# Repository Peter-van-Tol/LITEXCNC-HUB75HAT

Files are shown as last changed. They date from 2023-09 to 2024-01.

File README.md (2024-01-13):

# HUB75HAT

A PCB that turns the Colorlight 5A-75B into an easy to use CNC controller for cheap.

This project ist based on:
- [cyber-murmel/chubby-hat](https://github.com/cyber-murmel/chubby-hat)
- [3k/chubby75](https://github.com/q3k/chubby75/tree/master/5a-75b])

The [HUB75HAT](src/HUB75HAT) is 5A-75B motherboard host for a Raspberry Pi CPU. The HUB75HAT connects to the RPI’s GPIO interface and uses SPI for FPGA communication. Three 26 pin header connectors with standard parallel port pinouts and 5V tolerant I/O are provided for compatibility with most parallel port interfaced motion control / CNC breakout cards / multi axis step motor drives.

In addition to the parallel expansion ports, the HUB75HAT provides two RS-485 interfaces for I/O communication to other RS-485 applications, such as the Huanyang VFD series. These RS-485 are directly taken from the RPI’s header (UART0/1 and UART5).

The firmware is flashed onto the 5A-75B by using the RPI’s GPIO pins. There is no need for external programmers.

The motherboard can also be used _without_ the RPI, by using the standard ethernet communication of the 5A-75B. In this case one would loose the ability to use the RS-485 interfaces and an external tool will be required to flash new firmware.

## Breakout boards (BOB)
Breakout boards are available for the HUB75HAT. These BOBs are designed to add functionality to the HUB75HAT by
extending the GPIO from the 3 26 pin header connectors with drivers, receivers, opto-couplers, etc. Currently the
following BOBs are available:
- [BOB4AXIS](src/BOB4AXIS): Supports driving of 4 axis with differential output. Has inputs for the ALARM of the stepper
  drivers for each axis. Also has optocouplers for homing switches. The homing switches can be either NPN or PNP (selectable
  per axis). Adding this BOB would be enough to run a small 3 axis CNC machine with 1 slave axis.
- [BOB4ENCODER](src/BOB4ENCODER): Supports up to 4 encoders with index (5V only). Unused inputs can be used for generic
  IO. This board also has two connections for SERIAL boards, to further expand GPIO for your machine.

## Serial boards (SERIAL)
These boards are still under development. Goal is to extend GPIO with SPI expanders.

## Releases
The table below gives for each board the current status and the latest release. 

| board | latest release |
|---|---|
| HUB75HAT | [v1.2](src/HUB75HAT/releases/v1.2/) |
| HC245T_BYPASS | [v1.0](src/HC245T_BYPASS//releases/v1.0/) |
| BOB4AXIS | [v1.1](src/BOB4AXIS/releases/v1.1/) |
| BOB4ENCODER | [v1.0](src/BOB4ENCODER/releases/v1.0/) |

In each release folder you'll find a production folder with:
- a .zip-file which can be uploaded to your favorite PCB manufacturer
- a BOM;
- a position file for assembly (only verified for HUB75HAT, the rest is hand-soldered)

## KiCad Version
The following version of KiCad has been used to design the boards:
```
Application: KiCad x64 on x64
Version: 7.0.7, release build
Libraries:
    wxWidgets 3.2.2
    FreeType 2.12.1
    HarfBuzz 6.0.0
    FontConfig 2.14.1
    libcurl/7.88.1-DEV Schannel zlib/1.2.13

Platform: Windows 10 (build 19044), 64-bit edition, 64 bit, Little endian, wxMSW

Build Info:
    Date: Aug 19 2023 13:12:00
    wxWidgets: 3.2.2 (wchar_t,wx containers)
    Boost: 1.81.0
    OCC: 7.7.1
    Curl: 7.88.1-DEV
    ngspice: 40
    Compiler: Visual C++ 1936 without C++ ABI

Build settings:
    KICAD_SPICE=ON
```

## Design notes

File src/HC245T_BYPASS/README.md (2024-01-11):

# `hc245t-bypass`

This tiny board is useful to replace 74HC245T chips on Colorlight 5A-75B and 5A-75E boards.

Don't forget to select Flex board type on the order page!

## Rework

The board needs some rework to improve solderability. It's also possible to solder it "as is", but you can encounter shorts between the adjacent pins.

First, separate the boards from a panel. This can be done easily with scissors.

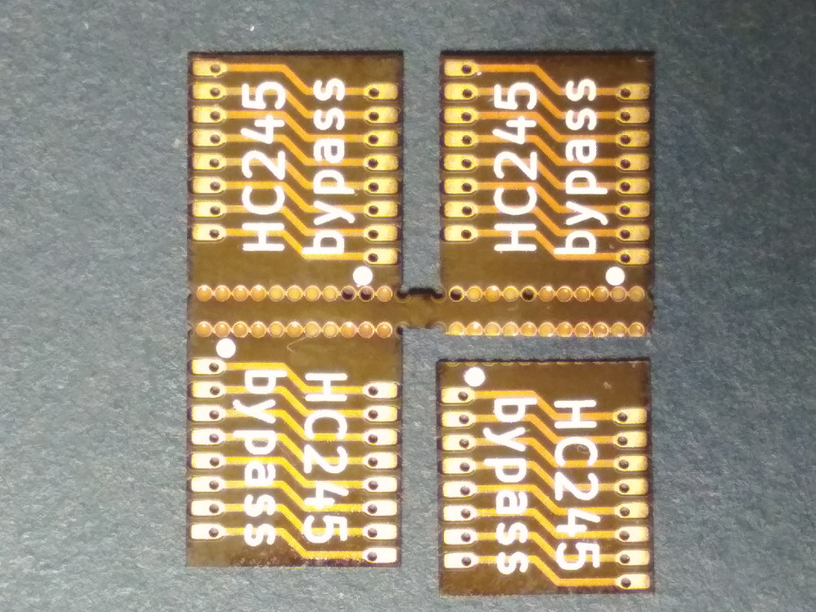
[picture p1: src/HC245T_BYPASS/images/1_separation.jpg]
Board separation


Next, cut each board by the line marked in red. The line should be on the edge of each via, not on the center. Try to make the line as straight as possible. The idea is to cut as much copper as possible, avoiding cutting most of the via copper.

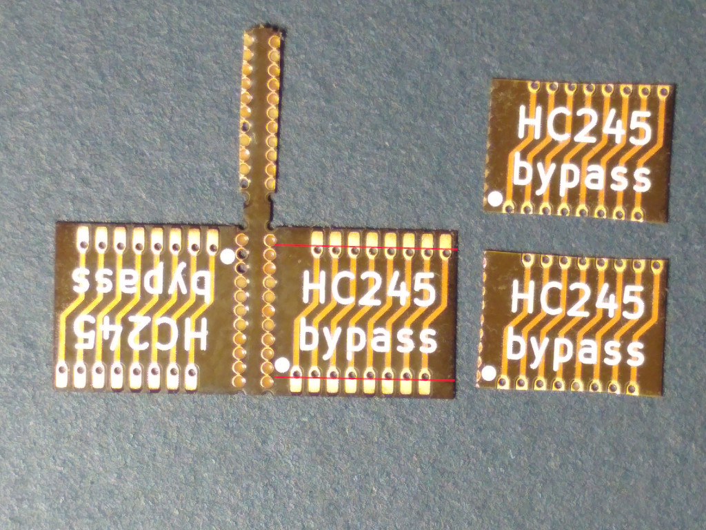
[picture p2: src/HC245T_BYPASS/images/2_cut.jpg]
Rework cut


Now solder it! Note that the first "pin" on the flex board corresponds to the second pin of the 74HC245T footpint.

You can also skip soldering about 50% of 74HC245T footprints by skipping footprints that are used for common signal (like A-E, CLK, LATCH, BLANK) distribution. You can learn in advance which footprints you need to solder and which not. Usually "color" signals are distributed through separate 74HC245T buffers located in groups of 3. Of course, this way you will not be able to control 8 signals out of... many, but it's still a good price for not soldering ~50% of tiny boards.

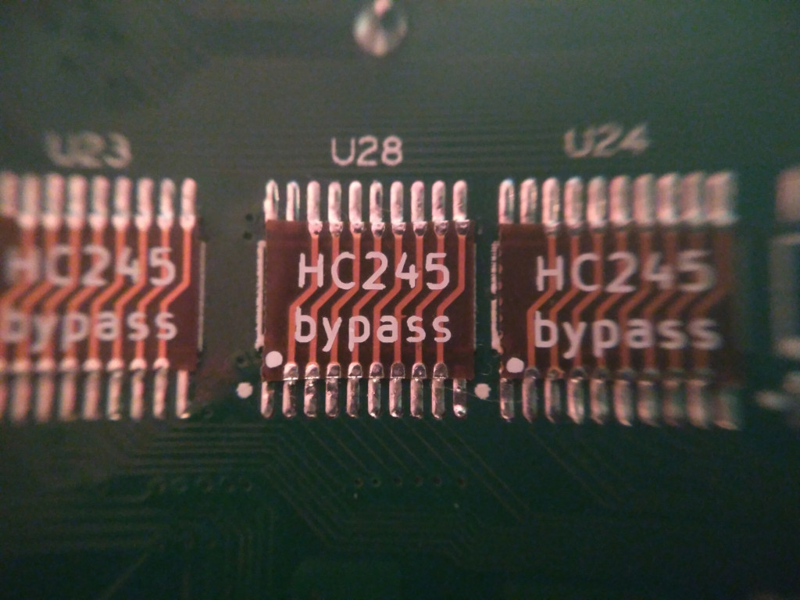
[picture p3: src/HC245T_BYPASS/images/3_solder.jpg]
Solder


Additionally, you can use a continuity tester to check that all "data" pins are connected and adjacent pins are not shorted accidentally. Some of the 74HC245T footpints used for common signal distribution have some of the pins connected together. Check twice: probably your "ringing" footprint has some signals connected on purpose.

## Original work

Shoutouts to [Tom Keddie](https://twitter.com/tom_keddie), who made the [first prototype](https://twitter.com/tom_keddie/status/1233759892164362241) with OSH Park flex board process. Unfortunately, castellated vias on OSH Park flex boards are not officially supported, and they do not guarantee correct manufacturing for such vias. The board in this repo is the improved version of the prototype with the following changes:

* Traces are on both sides of the board instead of only the top side.
* Castellated vias aren't used, instead they are made during the rework process.
* a lot of boards in a panel, instead of 2.
* Smaller silkscreen text that fits between the vias.

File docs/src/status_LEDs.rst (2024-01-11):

===========
Status LEDs
===========

LED locations
=============

The board has three groups of status LEDs:

#. Power and ENA on the bottom-left;
#. TX/RX for RS-489 connnection 1 (UART0/1)
#. TX/RX for RS-489 connnection 5 (UART5)

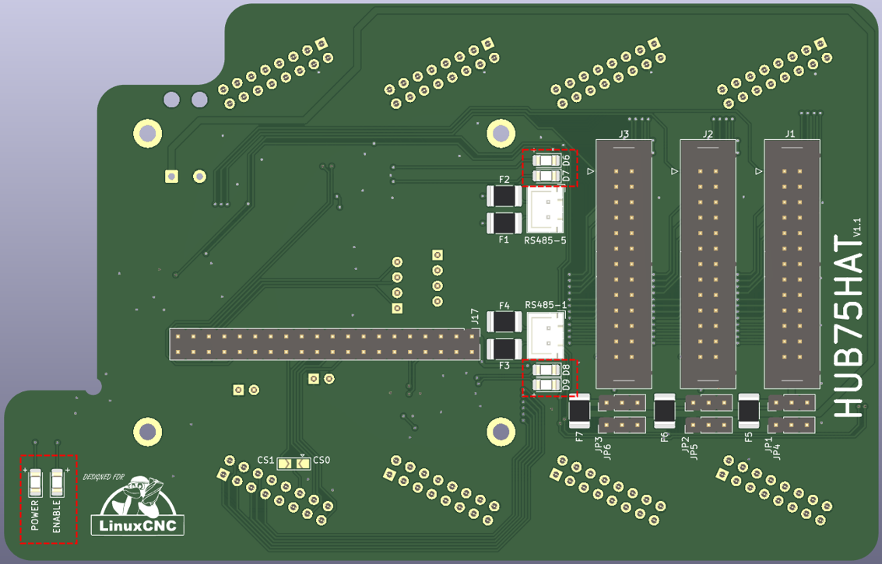
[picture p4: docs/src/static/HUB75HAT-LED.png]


Power, ENA and ESTOP
====================
The power indicator is on when power is supplied to the HUB75HAT (either by the RPi or the
5A-75B). When this LED is on, **DO NOT** unplug the GPIO connector, as this may lead to 
irreversible damage to the RPi and/or 5A-75B.

The ENA indicator is on when the board got the _enable_ command from LinuxCNC. When this LED 
is on, signals from the 5A-75B will flow to the three I/O connectors. It is strongly recommended
not to change connections from the I/O, as this may result in damage or unexpected movement of
the machine.

.. warning::
    In version 1.0 the ENA-LED is not working.

TX/RX status LEDs
=================
Both RS-485 connectors have two LEDs indicating communication to and from the port.

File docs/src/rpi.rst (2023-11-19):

===========================
Preparing your Raspberry-Pi
===========================

This sections describes the steps required to prepare your Raspberry-Pi for running 
LinuxCNC 2.8.4 with the HUB75HAT. You can also choose to use one of the ready-made
images, in which case you can skip these steps. The available images are listed in
the table below.

.. list-table:: Pre-built images for Raspberry-Pi
   :header-rows: 1

   * - Linux version
     - LinuxCNC version
     - username/password
     - link
     - remarks
   * - Debian Buster (32-bit)
     - LinuxCNC 2.8.4
     - cnc/linuxcnc
     - 
     -
   * - Debian Bookworm (64-bit)
     - LinuxCNC 2.9
     - cnc/tuxcnc
     - `link <https://drive.google.com/file/d/1PvfQPvsrcP9Ss2Zrryh35VmkFn31pA4P/view?usp=sharing>`_
     - Read text file on Desktop

Flashing a real-time OS
=======================

Follow these steps to install Debian Buster with a real-time kernel on your
Raspberry-Pi. This recipe has been `posted <https://forum.linuxcnc.org/9-installing-linuxcnc/47841-installing-linuxcnc-2-8-4-on-raspbian-10-buster-tested-on-raspberry-pi-3b-pi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>`_
on the LinuxCNC forum by *elovalvo*.

#. Download from `www.raspberrypi.com <https://www.raspberrypi.com/software/operating-systems/#raspberry-pi-os-legacy>`_
   an image of stable legacy version of Raspberry Pi OS Buster and install to a
   SD card (with Raspberry Pi Imager or similar).
#. Update the OS:

    .. code-block:: bash

        sudo apt update
        sudo apt upgrade

#. Install the realtime kernel (5.15.65-rt49) (source: https://github.com/kdoren/linux/releases):

    .. code-block:: bash

        sudo su     
        cd /tmp     
        wget https://github.com/kdoren/linux/releases/download/rpi_5.15.65-rt49/linux-image-5.15.65-rt49-v7l+_5.15.65-1_armhf.deb     
        apt install ./linux-image-5.15.65-rt49-v7l+_5.15.65-1_armhf.deb     
        KERN=5.15.65-rt49-v7l+      
        mkdir -p /boot/$KERN/o/     
        cp -d /usr/lib/linux-image-$KERN/overlays/* /boot/$KERN/o/     
        cp -dr /usr/lib/linux-image-$KERN/* /boot/$KERN/     
        [[ -d /usr/lib/linux-image-$KERN/broadcom ]] && cp -d /usr/lib/linux-image-$KERN/broadcom/* /boot/$KERN/     
        touch /boot/$KERN/o/README     
        mv /boot/vmlinuz-$KERN /boot/$KERN/     
        mv /boot/initrd.img-$KERN /boot/$KERN/     
        mv /boot/System.map-$KERN /boot/$KERN/     
        cp /boot/config-$KERN /boot/$KERN/     
        cp /boot/cmdline.txt /boot/$KERN/     
        cat >> /boot/config.txt << EOF     

        [all]     
        kernel=vmlinuz-$KERN     
        # initramfs initrd.img-$KERN     
        os_prefix=$KERN/     
        overlay_prefix=o/$(if [[ "$KERN" =~ 'v8' ]]; then echo -e "\narm_64bit=1"; fi)     
        [all]     
        EOF

#. Optimizing kernel (source: https://gnipsel.com/linuxcnc/rpi4-11-emc.html) by opening ``cmdline.txt``

    .. code-block:: bash

        sudo nano /boot/$KERN/cmdline.txt

   And adding ``isolcpus=,2,3 idle=poll`` to the end of the string. To close the file, press
   ``Ctrl+X``, ``y`` and ``Enter``.

We recommend restarting your Raspberry-Pi to ensure that the changes to take effect.

Installing LinuxCNC
===================

Follow these steps to install LinuxCNC 2.8.4. This recipe has been `posted <https://forum.linuxcnc.org/9-installing-linuxcnc/47841-installing-linuxcnc-2-8-4-on-raspbian-10-buster-tested-on-raspberry-pi-3b-pi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>`_
on the LinuxCNC forum by *elovalvo*.

#. Add the LinuxCNC Archive Signing Key to your apt keyring

    .. code-block:: bash

        sudo apt-key adv --keyserver hkp://keyserver.ubuntu.com --recv-key 3cb9fd148f374fef

#. Add the apt repository (`link <http://linuxcnc.org/docs/html/getting-started/getting-linuxcnc.html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>`_):

    .. code-block:: bash

        echo deb http://linuxcnc.org/ buster base 2.8-rtpreempt | sudo tee /etc/apt/sources.list.d/linuxcnc.list
        echo deb-src http://linuxcnc.org/ buster base 2.8-rtpreempt | sudo tee -a /etc/apt/sources.list.d/linuxcnc.list

#. Update the package list from linuxcnc.org and install LinuxCNC

    .. code-block:: bash
        
        sudo apt-get update
        sudo apt-get install linuxcnc-uspace linuxcnc-uspace-dev

Installing LiteX-CNC
====================

Litex-CNC can be installed using ``pip``:

.. code-block:: bash
    
    pip3 install litexcnc[cli] --user

.. note::
    The suffix ``[cli]`` is required to install the command-line interface. Without
    this suffix the scripts referenced in this documentation will not work.

To install the Litex-CNC driver for LinuxCNC, use the following command:

.. code-block:: bash
    
    sudo env "PATH=$PATH" litexcnc install_driver

Optionally, one can also install the toolchain required to build the firmware on the
Raspberry-Pi. When this step is omitted, the firmware has to be compiled on a different
computer.

.. code-block:: bash
    
    litexcnc install_toolchain --user --architecture arm --os linux

.. note::
    This description is specific for Debian Buster, which is a 32-bit operating system.
    When using a newer version of Debian, it might be a 64-bit version, in which case
    the switch ``--architecture arm64`` should be used instead. You can check whether
    you have a 32-bit or a 64-bit operating system by running ``uname -a`` in the terminal.

Enabling SPI
============

The SPI peripheral is not turned on by default. There are two methods to adjust
the settings, either by using the command-line (``raspi-config``) or by using the
GUI.

Using the Desktop GUI
---------------------

You can use the Desktop GUI by heading to the **Pi Start Menu** > **Preferences** > 
**Raspberry Pi Configuration**.

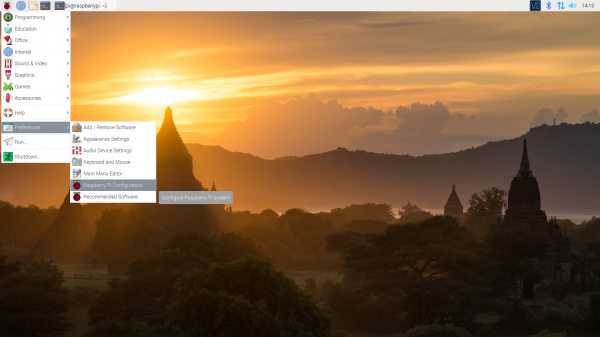
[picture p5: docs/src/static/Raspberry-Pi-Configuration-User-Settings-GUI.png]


A window will pop up with different tabs to adjust settings. What we are interested
is the Interfaces tab. Click on the tab and select Enable for SPI. At this point, you
can enable additional interfaces depending on your project needs. Click on the OK
button to save.

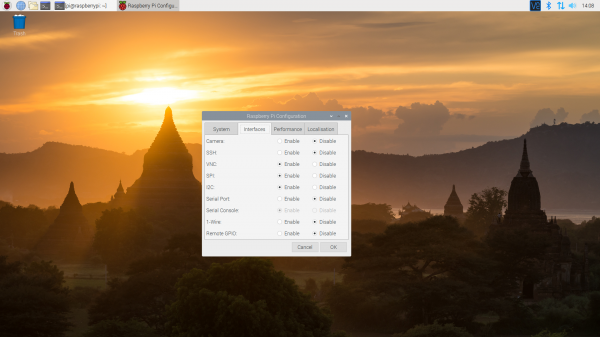
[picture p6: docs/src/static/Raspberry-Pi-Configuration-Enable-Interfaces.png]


We recommend restarting your Pi to ensure that the changes to take effect. Click on 
the **Pi Start Menu** > **Preferences** > **Shutdown**. Since we just need to restart,
click on the Restart button.

Using the command-line
----------------------

If you are using a terminal, you will need to:

#. Run ``sudo raspi-config``.
#. Use the down arrow to select 5 Interfacing Options
#. Arrow down to ``P4 SPI``.
#. Select yes when it asks you to enable SPI,
#. Also select yes if it asks about automatically loading the kernel module.
#. Use the right arrow to select the <Finish> button.
#. Select yes when it asks to reboot.

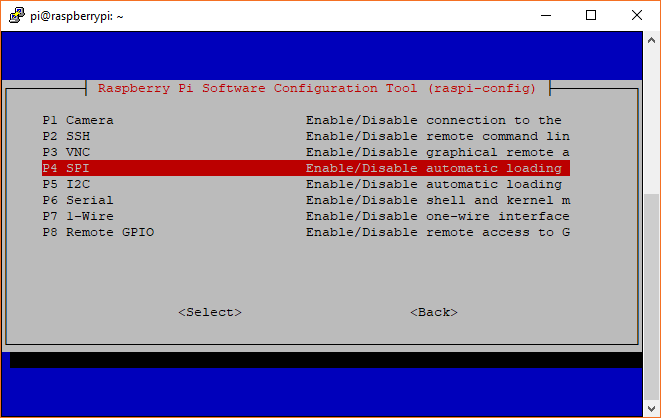
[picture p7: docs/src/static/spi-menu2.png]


The system will reboot. When it comes back up, log in and enter the following command:

.. code-block:: bash

    ls /dev/*spi*

The Pi should respond with::

    /dev/spidev0.0  /dev/spidev0.1

These represent SPI devices on chip enable pins 0 and 1, respectively. These pins are
hardwired within the Pi. Ordinarily, this means the interface supports at most two 
peripherals, but there are cases where multiple devices can be daisy-chained, sharing
a single chip enable signal.

Enabling UART
=============
THe HUB75HAT has two RS-485 connectors, which are powered by the RaspeberryPi UARTs 
0 and 5. To use the RS-485 communication additional steps are required.

UART0
-----

.. info::
    Enabling UART5 is easier than enabling UART1. It is only recommended to enable UART0
    when two RS-485 connections are required.

By default, the primary UART is assigned to the Linux console. If you wish to use the
primary UART for other purposes, you must reconfigure Raspberry Pi OS. This can be done
by using raspi-config:

#. Start raspi-config: ``sudo raspi-config``.
#. Select option 3 - Interface Options.
#. Select option P6 - Serial Port.
#. At the prompt *Would you like a login shell to be accessible over serial?* answer 'No'
#. At the prompt *Would you like the serial port hardware to be enabled?* answer 'Yes'
#. Exit raspi-config and reboot the Raspberry Pi for changes to take effect.

To switch the Bluetooth function to use the mini UART, and makes the first PL011 (UART0) 
the primary UART, add the following lines to ``/boot/config.txt``:

.. code-block::

    enable_uart=1
    dtoverlay=miniuart-bt
    core_freq=250

After rebooting the RaspeberryPi, one can check the whether messages can be sent using UART0
by sending a test-message:

.. code-block:: shell

   sudo echo "Hello world" > /dev/ttyAMA0

Sometimes one can experience ``Permission denied`` problems when executing the command above. In
this case there is most likely another process using UART0. One can disable this service by running
the following command and rebooting the RaspberryPi.

.. code-block:: shell

    sudo systemctl mask serial-getty@ttyAMA0.service

UART5
-----
UART5 is located on GPIO pins 12 (RX) and 13 (TX). To enable UART5 add the following
line to ``/boot/config.txt``:

.. code-block::

    dtoverlay=uart5

UART5 can be found under ``/dev/ttyAMA1``.

Example usage
-------------
An example usage of the UARTs is the `non-realtime component for Huanyang VFDs <https://linuxcnc.org/docs/html/man/man1/hy_vfd.1.html>`_.

.. code-block::

    hy_vfd --device /dev/ttyAMA1

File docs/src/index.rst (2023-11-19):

=================
LITEXCNC-HUB75HAT
=================

A PCB that turns the Colorlight 5A-75B into an easy to use CNC motion controller for cheap. This 
project is based on `q3k/chubby75 <https://github.com/q3k/chubby75/tree/master/5a-75b>`_ and 
`LitexCNC <https://github.com/Peter-van-Tol/LiteX-CNC>`_.

The HUB75HAT is 5A-75B motherboard host for a Raspberry Pi CPU. The HUB75HAT connects to the RPI's
GPIO interface and uses SPI for FPGA communication. Three 26 pin header connectors with standard
parallel port pinouts and 5V tolerant I/O are provided for compatibility with most parallel port 
interfaced motion control / CNC breakout cards / multi axis step motor drives.

In addition to the parallel expansion ports, the HUB75HAT provides two RS-485 interfaces for I/O 
communication to other RS-485 applications, such as the Huanyang VFD series. These RS-485 are directly
taken from the RPI's header (UART0 and UART1).

The firmware is flashed onto the 5A-75B by using the RPI's GPIO pins. There is no need for external
programmers. 

The motherboard can also be used *without* the RPI, by using the standard ethernet communication
of the 5A-75B. In this case one would loose the ability to use the RS-485 interfaces and an external
tool will be required to flash new firmware. 

Contents
========

.. toctree::
   :maxdepth: 2

   Connectors <connectors>
   Status LEDs <status_LEDs>
   Preparing your 5A-75B <5a-75b>
   Preparing your Raspberry-Pi <rpi>
   License <license>
   Changelog <changelog>

Indices and tables
==================

* :ref:`genindex`
* :ref:`modindex`
* :ref:`search`

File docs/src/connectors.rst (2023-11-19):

==========
Connectors
==========

Connector locations
===================

The board contains the following connectors:

- power connector for connecting the HUB75HAT and the 5A-75B
- three connectors for I/O (``J1```, ``J2``, and ``J3``). For each connector one can
  select pull-up or pull-down resistors and whether power should be supplied over the
  connector.
- two RS-485 connectors.



Power
=====
The board can be powered in two ways:

- via the USB-C power supply of the RaspberryPi;
- via the external 5V supply of the 5A-75B.

.. warning::
   When the RaspberryPi and 5A-75B are both powered seperately, the link between the
   HUB75HAT and the 5A-75B should not be connected!

In both cases the 5V supply is shared between the RaspberryPi and the 5A75B via
the link in the top left corner of the board and the GPIO header of the Pi. The
pinout of the power header is:

- pin 1 (located closed to the edge of the board): +5V
- pin 2: GND

I/O Connector pinout
====================
Three 26 pin header connectors with standard parallel port pinouts and 5V tolerant 
I/O are provided for compatibility with most parallel port interfaced motion control / 
CNC breakout cards / multi axis step motor drives.

.. note::
    The FPGA used on the 5a-75B has a 3.3V absolute maximum input voltage specification. 
    To allow interfacing with 5V inputs, the HUB75HAT has bus switches on all I/O pins
    to provide 5V tolerance (`SN74CB3T3245 <https://www.ti.com/product/SN74CB3T3245>`_).

    Note that even though the HUB75HAT can tolerate 5V signal inputs, its outputs will not
    swing to 5V. The outputs are push pull CMOS that will drive to the output supply rail of
    3.3V. This is sufficient for TTL compatibility but may cause problems with some types of
    loads. For example when driving an LED that has its anode connected to 5V, in such
    devices as OPTO isolators and I/O module rack SSRs, the 3.3V high level may not
    completely turn the LED off. To avoid this problem, either drive loads that are ground
    referred, Use 3.3V as the VCC for VCC referred loads, or use open drain mode.

.. warning::
    After power-up or system reset and before the FPGA is configured, the per connector
    pull-up or pull-down resistors will pull all I/O signals per connector to a high or 
    low level. If the FPGA is used for motion control or controlling devices that could 
    present a hazard when enabled, external circuitry should be designed so that this 
    initial state results in a safe condition.

.. csv-table:: Connector I/O-1
   :file: ./tables/IO1.csv
   :widths: 12, 12, 12, 12, 4, 12, 12, 12, 12 
   :header-rows: 1

.. csv-table:: Connector I/O-2
   :file: ./tables/IO2.csv
   :widths: 12, 12, 12, 12, 4, 12, 12, 12, 12 
   :header-rows: 1

.. csv-table:: Connector I/O-3
   :file: ./tables/IO3.csv
   :widths: 12, 12, 12, 12, 4, 12, 12, 12, 12 
   :header-rows: 1

Selection pull-up / pull-down
----------------------------- 
Each I/O connector on the HUB75HAT can have its I/O termination resistors set to pull-up
or pull-down mode. These resistors set the I/O voltage level when the pins are not driven
by the FPGA.

.. info::
   It may be desirable with some parallel port type breakout boards to choose the pulldown
   mode, so that the FPGA outputs are in the low state at power up.

Connector 5V power
------------------ 
The HUB75HAT has the option to supply 5V power to the breakout board. This option is
added to simplify wiring. The option uses 4 parallel cable signals that are normally
used as grounds for supplying 5V to the remote breakout board (DB25 pins 22,23,24 and
25). These pins are AC bypassed on both the HUB75HAT and the breakout cards so do not
compromise AC signal integrity.

The 5V power option is individually selectable for each of the three I/O connectors.
The breakout 5V power is protected by per connector PTC devices (300 mA trip) so will
not cause damage to the HUB75HAT or system if accidentally shorted. This option should
only be enabled for breakout boards or boards specifically wired to accept 5V power on
DB25 pins 22 through 25.

RS-485
======

TODO

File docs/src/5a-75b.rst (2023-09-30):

=====================
Preparing your 5A-75B
=====================

The 5A-75B needs to be modified before it can be used as a CNC motion controller.
The most important changes are:

#. Adding pins for flashing the firmware onto the card (JTAG);
#. Removing the buffers.

Especially the last step requires the removal of several SMD-components from the
card and migth require some experience with soldering these types of components.

Board overview
==============

The image below shows an annotated view of the PCB, showing the JTAG-headers and
the buffers. At this moment there are three known versions of these cards: v6.1,
v7.0 and v8.0. The layout of these cards may differ between versions.

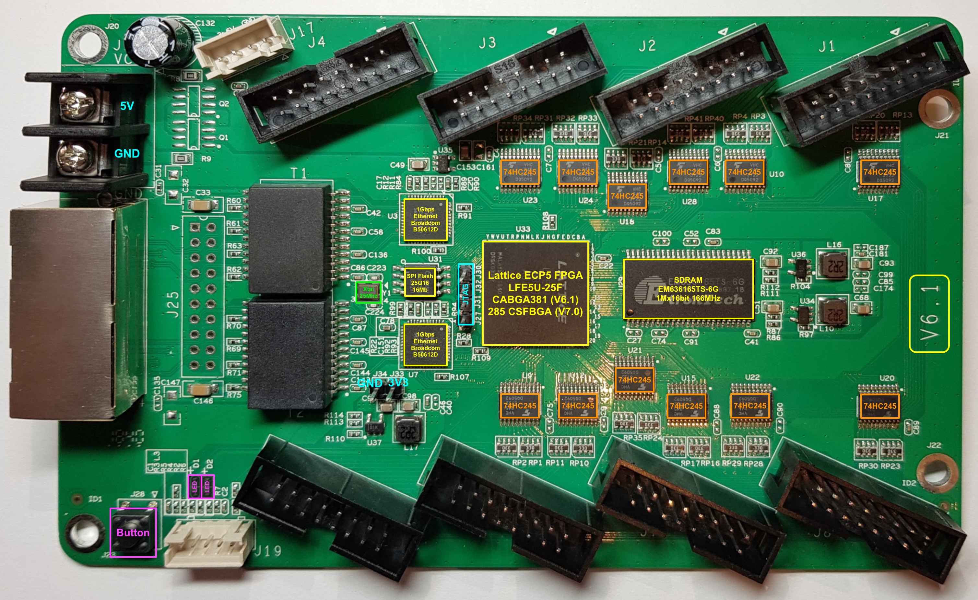
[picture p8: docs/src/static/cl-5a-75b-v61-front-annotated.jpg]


The main difference of the V8.0 card is the location of the JTAG-headers. The HUB75HAT
is designed to accept all versions.

Adding JTAG-headers
===================

The JTAG headers are not populated by default. Solder a 2-pin header at J33/J34 and
a 4-pin header for JTAG next to the FPGA (J27, J31, J32, J30). For the function of
each of the pins, see the `hardware description <https://github.com/q3k/chubby75/blob/master/5a-75b/README.md>`.

Removing the buffers
====================

.. warning::
    All buffers on the board convert the 3.3 V from the FPGA to 5V outputs. Leaving
    the wrong buffers on the board might drive the Raspberry-Pi GPIO with 5 V, leading
    to destruction of the Raspberry-Pi. Therefore it is strongly recommended to remove
    all buffers from the 5A-75B. The HUB75HAT is designed to run on 3.3 V and provides
    5V tolerant buffers in order to protect the FPGA.

The buffers can be removed by any of the methods below:

- desoldering;
- cutting the legs of the ICs with a sharp knife and clearing the pads from the
  left-over pins.

One has to be very carefull

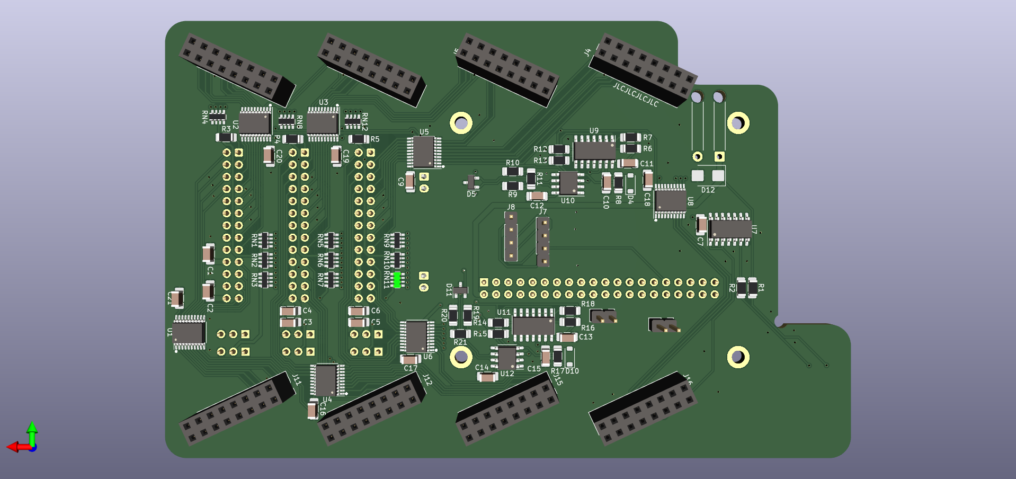
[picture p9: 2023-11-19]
images/LITEXCNC-HUB75HAT_back.png

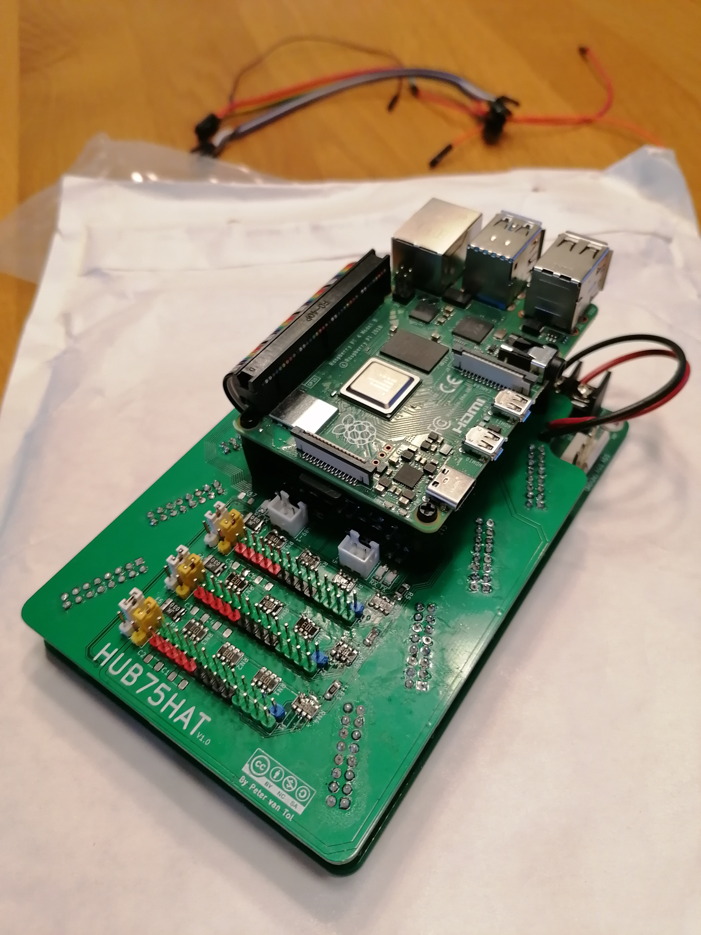
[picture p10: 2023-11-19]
images/HUB75HAT-v1.0.jpg

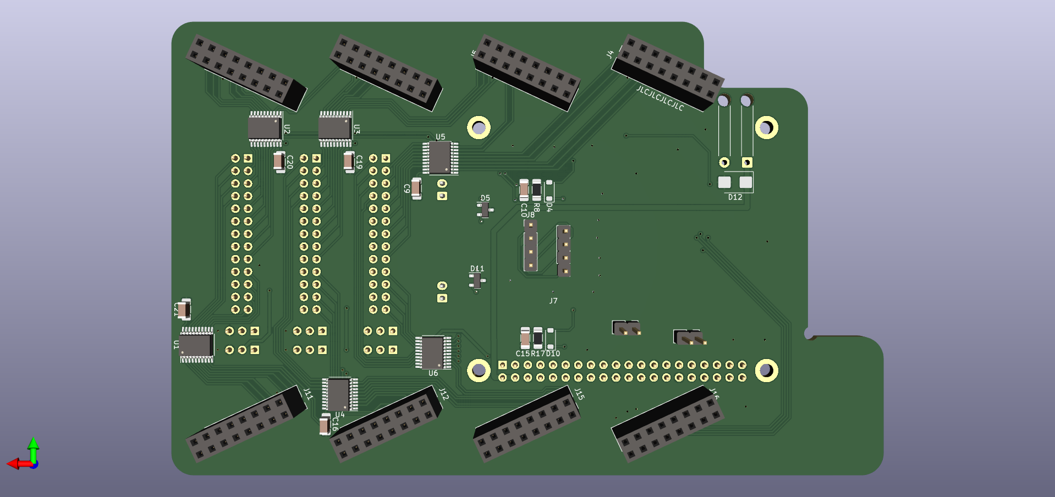
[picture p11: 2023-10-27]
docs/src/images/LITEXCNC-HUB75HAT-back.png

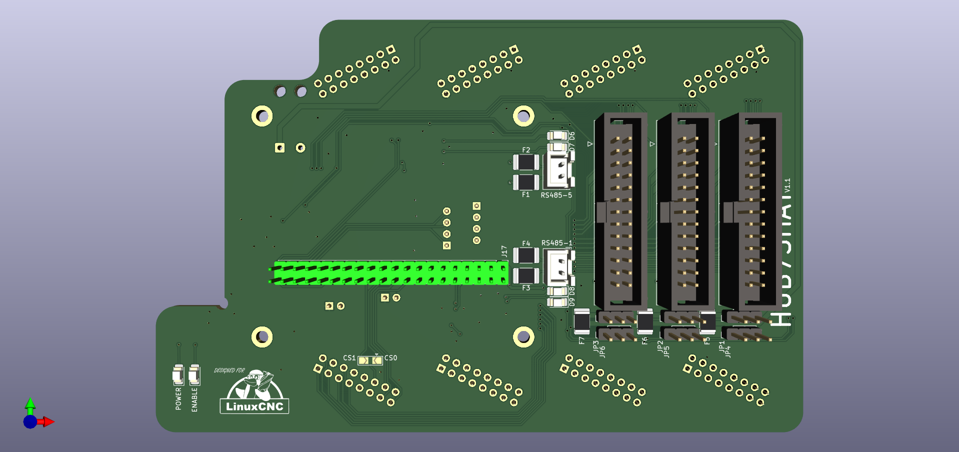
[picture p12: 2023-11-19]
images/LITEXCNC-HUB75HAT_front.png

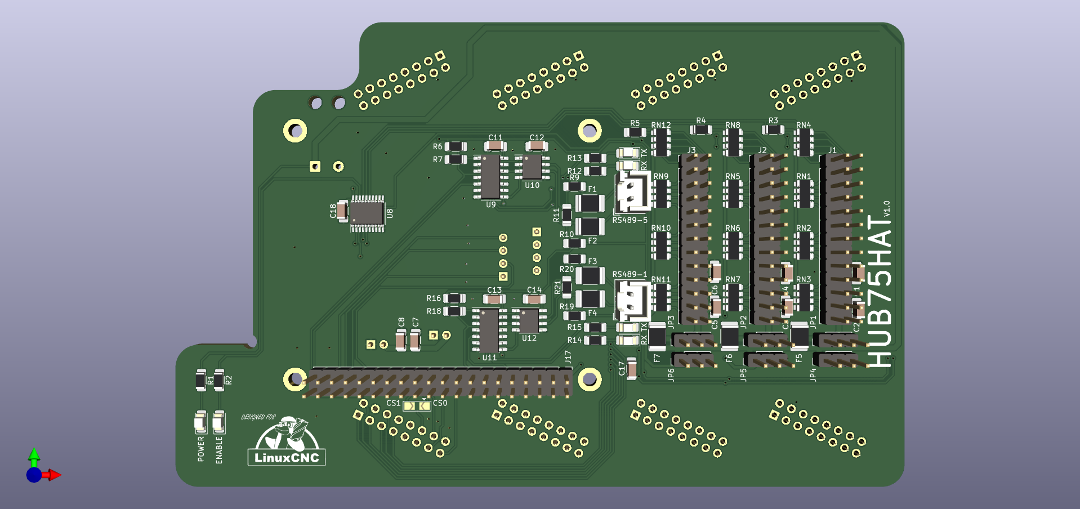
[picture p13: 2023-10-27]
docs/src/images/LITEXCNC-HUB75HAT-front.png

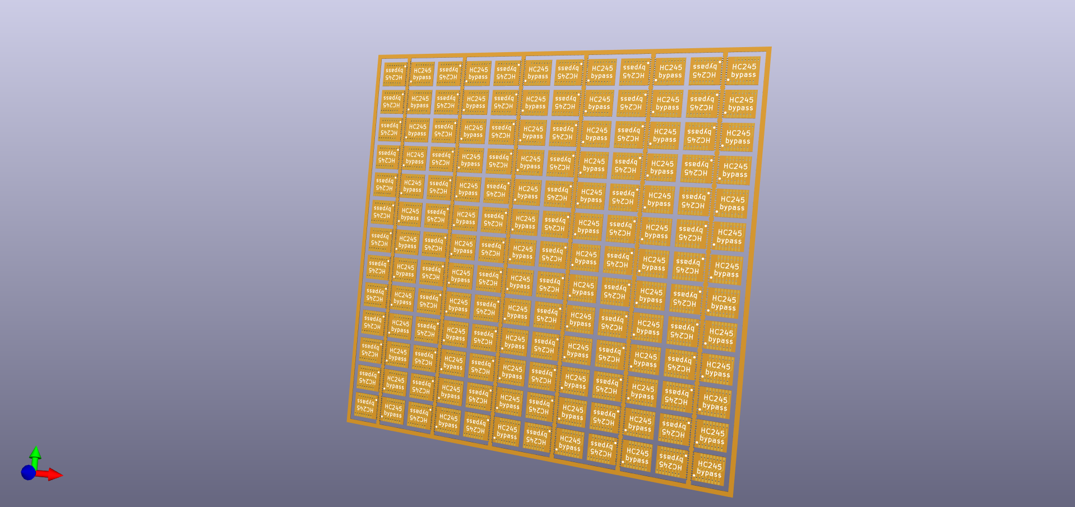
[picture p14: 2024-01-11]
src/HC245T_BYPASS/KICAD/hc245t-bypass-panel.png

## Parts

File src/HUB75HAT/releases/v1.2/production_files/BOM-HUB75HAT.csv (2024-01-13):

Comment | Designator | Footprint | LCSC
74CB3T3245 | U1,U2,U3,U4,U5,U6,U8 | TSSOP-20_4.4x6.5mm_P0.65mm | C15298
33pF | C10,C15 | C_0603_1608Metric_Pad1.08x0.95mm_HandSolder | C1663
150 | R12,R13,R14,R15,R2 | R_0805_2012Metric_Pad1.20x1.40mm_HandSolder | C17471
300 | R1 | R_0805_2012Metric_Pad1.20x1.40mm_HandSolder | C17617
R | R3,R4,R5 | R_1206_3216Metric_Pad1.30x1.75mm_HandSolder | C17902
120 | R11,R21 | R_1206_3216Metric_Pad1.30x1.75mm_HandSolder | C17909
4.7K | R10,R16,R18,R19,R20,R6,R7,R9 | R_1206_3216Metric_Pad1.30x1.75mm_HandSolder | C17936
56k | R17,R8 | R_0603_1608Metric_Pad0.98x0.95mm_HandSolder | C23206
100nF | C1,C11,C12,C13,C14,C16,C17,C18,C19,C2,C20,C21,C3,C4,C5,C6,C7,C9 | C_1206_3216Metric_Pad1.33x1.80mm_HandSolder | C24497
SM712_SOT23 | D11,D5 | SOT-23 | C2687124
CN1J4KTTD1002F | RN1,RN10,RN11,RN12,RN2,RN3,RN4,RN5,RN6,RN7,RN8,RN9 | R_Array_Convex_4x0603_handsolder | C29718
108L | F1,F2,F3,F4,F5,F6,F7 | Fuse_1812_4532Metric_Pad1.30x3.40mm_HandSolder | C782760
MAX3485 | U10,U12 | SOIC-8_3.9x4.9mm_P1.27mm | C8963
Conn_02x20_Odd_Even | J17 | IDC-Header_2x20_P2.54mm_Vertical
Conn_02x13_Odd_Even | J2 | IDC-Header_2x13_P2.54mm_Vertical
LED | D9 | LED_1206_3216Metric_Pad1.42x1.75mm_HandSolder
Jumper_3_Open | JP6 | PinHeader_1x03_P2.54mm_Vertical
LED | D1 | LED_1206_3216Metric_Pad1.42x1.75mm_HandSolder
LED | D6 | LED_1206_3216Metric_Pad1.42x1.75mm_HandSolder
Jumper_3_Open | JP4 | PinHeader_1x03_P2.54mm_Vertical
Jumper_3_Open | JP1 | PinHeader_1x03_P2.54mm_Vertical
LED | D2 | LED_1206_3216Metric_Pad1.42x1.75mm_HandSolder
Jumper_3_Open | JP3 | PinHeader_1x03_P2.54mm_Vertical
SolderJumper_3_Open | JP7 | SolderJumper-3_P2.0mm_Open_TrianglePad1.0x1.5mm
LED | D7 | LED_1206_3216Metric_Pad1.42x1.75mm_HandSolder
Jumper_3_Open | JP5 | PinHeader_1x03_P2.54mm_Vertical
Jumper_3_Open | JP2 | PinHeader_1x03_P2.54mm_Vertical
Conn_02x13_Odd_Even | J3 | IDC-Header_2x13_P2.54mm_Vertical
Conn_02x13_Odd_Even | J1 | IDC-Header_2x13_P2.54mm_Vertical
LED | D8 | LED_1206_3216Metric_Pad1.42x1.75mm_HandSolder
1N4148W | D4 | D_SOD-123
V8.0 | J14 | PinHeader_1x02_P2.54mm_Vertical
74HC04 | U7 | SOIC-14_3.9x8.7mm_P1.27mm
v8.0 | J8 | PinHeader_1x04_P2.54mm_Vertical
HUB75 | J4 | PinSocket_2x08_P2.54mm_Vertical
V7.0 | J13 | PinHeader_1x02_P2.54mm_Vertical
HUB75 | J12 | PinSocket_2x08_P2.54mm_Vertical
HUB75 | J11 | PinSocket_2x08_P2.54mm_Vertical
74HC04 | U9 | SOIC-14_3.9x8.7mm_P1.27mm
74HC04 | U11 | SOIC-14_3.9x8.7mm_P1.27mm
1N4148W | D10 | D_SOD-123
HUB75 | J6 | PinSocket_2x08_P2.54mm_Vertical
HUB75 | J15 | PinSocket_2x08_P2.54mm_Vertical
v7.0 | J7 | PinHeader_1x04_P2.54mm_Vertical
HUB75 | J16 | PinSocket_2x08_P2.54mm_Vertical
Conn_01x02 | J10 | SolderWire-0.5sqmm_1x02_P4.6mm_D0.9mm_OD2.1mm_Relief
HUB75 | J5 | PinSocket_2x08_P2.54mm_Vertical
HUB75 | J9 | PinSocket_2x08_P2.54mm_Vertical

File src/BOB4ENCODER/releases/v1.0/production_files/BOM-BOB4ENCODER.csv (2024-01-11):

Comment | Designator | Footprint | LCSC
Conn_02x04_Odd_Even | J6 | PinSocket_2x04_P1.27mm_Horizontal
Conn_02x04_Odd_Even | J7 | PinSocket_2x04_P1.27mm_Horizontal
Screw_Terminal_01x08 | J5 | CONN-TH_8P-P5.08_KF142V-5.08-8P
Jumper_2_Open | JP2 | PinHeader_1x02_P2.54mm_Vertical
Jumper_2_Open | JP7 | PinHeader_1x02_P2.54mm_Vertical
Jumper_2_Open | JP1 | PinHeader_1x02_P2.54mm_Vertical
Screw_Terminal_01x08 | J3 | CONN-TH_8P-P5.08_KF142V-5.08-8P
Jumper_2_Open | JP9 | PinHeader_1x02_P2.54mm_Vertical
Jumper_2_Open | JP11 | PinHeader_1x02_P2.54mm_Vertical
Jumper_2_Open | JP12 | PinHeader_1x02_P2.54mm_Vertical
Jumper_2_Open | JP3 | PinHeader_1x02_P2.54mm_Vertical
MountingHole_Pad | H3 | MountingHole_3.2mm_M3_Pad_Via
MountingHole_Pad | H1 | MountingHole_3.2mm_M3_Pad_Via
Jumper_2_Open | JP10 | PinHeader_1x02_P2.54mm_Vertical
MountingHole_Pad | H4 | MountingHole_3.2mm_M3_Pad_Via
Screw_Terminal_01x08 | J2 | CONN-TH_8P-P5.08_KF142V-5.08-8P
Screw_Terminal_01x08 | J4 | CONN-TH_8P-P5.08_KF142V-5.08-8P
MountingHole_Pad | H2 | MountingHole_3.2mm_M3_Pad_Via
Jumper_2_Open | JP4 | PinHeader_1x02_P2.54mm_Vertical
Jumper_2_Open | JP5 | PinHeader_1x02_P2.54mm_Vertical
Conn_02x13_Odd_Even | J1 | IDC-Header_2x13_P2.54mm_Vertical
Jumper_2_Open | JP8 | PinHeader_1x02_P2.54mm_Vertical
Jumper_2_Open | JP6 | PinHeader_1x02_P2.54mm_Vertical
AM26LV32xD | U2 | SOIC-16_3.9x9.9mm_P1.27mm
AM26LV32xD | U3 | SOIC-16_3.9x9.9mm_P1.27mm
0.1uF | C3 | C_1206_3216Metric_Pad1.33x1.80mm_HandSolder
AM26LV32xD | U1 | SOIC-16_3.9x9.9mm_P1.27mm
MMSZ5222BT1G | D1 | D_SOD-123
R | R1 | R_1206_3216Metric_Pad1.30x1.75mm_HandSolder
Polyfuse_Small | F1 | R_1812_4532Metric_Pad1.30x3.40mm_HandSolder
0.1uF | C2 | C_1206_3216Metric_Pad1.33x1.80mm_HandSolder
0.1uF | C1 | C_1206_3216Metric_Pad1.33x1.80mm_HandSolder

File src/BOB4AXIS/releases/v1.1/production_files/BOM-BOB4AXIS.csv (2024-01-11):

Comment | Designator | Footprint | LCSC
0.1uF | C1,C2,C3,C4 | C_1206_3216Metric_Pad1.33x1.80mm_HandSolder | C24497
KF142V-5_08-2P | U7 | CONN-TH_P5.08_KF142V-5.08-2P | C475134
AM26LS31CD | U5,U6,U9 | SOIC-16_3.9x9.9mm_P1.27mm | C6179
74HC86 | U8 | SOIC-14_3.9x8.7mm_P1.27mm | C6763
Screw_Terminal_01x08 | J5 | CONN-TH_8P-P5.08_KF142V-5.08-8P
MountingHole_Pad | H3 | MountingHole_3.2mm_M3_Pad_Via
Jumper_3_Open | JP6 | PinHeader_1x03_P2.54mm_Vertical
Screw_Terminal_01x08 | J8 | CONN-TH_8P-P5.08_KF142V-5.08-8P
Jumper_3_Open | JP3 | PinHeader_1x03_P2.54mm_Vertical
Jumper_3_Open | JP8 | PinHeader_1x03_P2.54mm_Vertical
Screw_Terminal_01x03 | J1 | CONN-TH_3P-P5.08_KF142V-5.08-3P
LTV-814 | U3 | DIP-4_W7.62mm
MountingHole_Pad | H1 | MountingHole_3.2mm_M3_Pad_Via
LTV-814 | U1 | DIP-4_W7.62mm
Screw_Terminal_01x08 | J6 | CONN-TH_8P-P5.08_KF142V-5.08-8P
Conn_02x13_Odd_Even | J9 | IDC-Header_2x13_P2.54mm_Vertical
Jumper_3_Open | JP2 | PinHeader_1x03_P2.54mm_Vertical
Jumper_3_Open | JP7 | PinHeader_1x03_P2.54mm_Vertical
Jumper_3_Open | JP4 | PinHeader_1x03_P2.54mm_Vertical
Screw_Terminal_01x03 | J4 | CONN-TH_3P-P5.08_KF142V-5.08-3P
Screw_Terminal_01x03 | J2 | CONN-TH_3P-P5.08_KF142V-5.08-3P
LTV-814 | U4 | DIP-4_W7.62mm
MountingHole_Pad | H2 | MountingHole_3.2mm_M3_Pad_Via
Jumper_3_Open | JP1 | PinHeader_1x03_P2.54mm_Vertical
MountingHole_Pad | H4 | MountingHole_3.2mm_M3_Pad_Via
Screw_Terminal_01x08 | J7 | CONN-TH_8P-P5.08_KF142V-5.08-8P
Screw_Terminal_01x03 | J3 | CONN-TH_3P-P5.08_KF142V-5.08-3P
Jumper_3_Open | JP5 | PinHeader_1x03_P2.54mm_Vertical
LTV-814 | U2 | DIP-4_W7.62mm
10k | R10 | R_1206_3216Metric_Pad1.30x1.75mm_HandSolder
1k | R1 | R_1206_3216Metric_Pad1.30x1.75mm_HandSolder
R | R7 | R_1206_3216Metric_Pad1.30x1.75mm_HandSolder
Polyfuse_Small | F1 | R_1812_4532Metric_Pad1.30x3.40mm_HandSolder
1k | R5 | R_1206_3216Metric_Pad1.30x1.75mm_HandSolder
10k | R12 | R_1206_3216Metric_Pad1.30x1.75mm_HandSolder
10k | R8 | R_1206_3216Metric_Pad1.30x1.75mm_HandSolder
10k | R11 | R_1206_3216Metric_Pad1.30x1.75mm_HandSolder
10k | R4 | R_1206_3216Metric_Pad1.30x1.75mm_HandSolder
10k | R2 | R_1206_3216Metric_Pad1.30x1.75mm_HandSolder
10k | R6 | R_1206_3216Metric_Pad1.30x1.75mm_HandSolder
10k | R9 | R_1206_3216Metric_Pad1.30x1.75mm_HandSolder
1k | R3 | R_1206_3216Metric_Pad1.30x1.75mm_HandSolder
10k | R13 | R_1206_3216Metric_Pad1.30x1.75mm_HandSolder

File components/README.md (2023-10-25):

# Components

This folder contains the parts which are downloaded from third-party resources. A good
source of parts is (https://jlcpcb.com/parts). Parts from this website can be downloaded
and converted to KiCAD using the Python tool `JLC2KiCadLib`:

``` shell
poetry run JLC2KiCadLib C475134  -dir AliExpress -symbol_lib AliExpressSymbols
```

Above statement will:
- download the part `C475134`;
- into the folder `AliExpress`;
- into the symbol file `AliExpressSymbols`.

See for more information the [documentation](https://github.com/TousstNicolas/JLC2KiCad_lib)
of `JLC2KiCadLib`.

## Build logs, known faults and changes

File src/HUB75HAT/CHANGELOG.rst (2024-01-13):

=========
CHANGELOG
=========

Version 1.2 (current version)
=============================

During soldering the version 1.1 boards, the following issues have been identified and solved in this version:
- The 40-pin header has the wrong footprint, there fore it clashes in practice with two polyfuses. The footprint
  will be corrected and the polyfuses will be moved to make space for the 40-pin header.
- Several markings on the board are missing. These will be added to the board.
- Removed unused diode from the board.

Version 1.1
===========

First production version of the board. In total 15 boards were ordered from JLCPCB. The boards were assembled by JLCPCB as well.
The total cost per board was around €17.50 (including shipping and taxes).

The board features:
- Designed for Raspberry Pi 4 and 5 (the older version RPi 3 might also work) with SPI communication
- 3 I/O connectors:
  - each 17 pins of freely addressable inputs / outputs;
  - selectable 10 kOhm pull-down or pull-up resistor;
  - optional 5V power supply on the connector;
- 2 RS-485 connectors for external communications (based on UART0 and UART5 on the Raspberry Pi);
- Resolved issues of board v1.0;
- re-designed with most of the components on the bottom side of the board. This makes the board cheaper to
  produce with services such as JLCPCB. The components to be soldered by hand are on the top side of the board,
  and are limited to: 6 LED's (size 1206), 7 polyfuses (size 1812) and the connectors. 

Version 1.0
===========

Initial version of the board. 

The board features:
- Designed for Raspberry Pi 4 and 5 (the older version RPi 3 might also work) with SPI communication
- 3 I/O connectors:
  - each 17 pins of freely addressable inputs / outputs;
  - selectable 10 kOhm pull-down or pull-up resistor;
  - optional 5V power supply on the connector;
- 2 RS-485 connectors for external communications (based on UART0 and UART5 on the Raspberry Pi)

![HUB75HAT](/images/HUB75HAT-v1.0.jpg)

Known issues:
- the space around the 40 pin connector of the HAT is a bit tight with the mounting points of the RPi. The solution to work with the current board is to use plastic stand-offs and cut part of these away.
- the enable signal should be inverted on the board, because the buffer Output Enable (`OE`) is active LOW. I rather send a HIGH signal to the board to enable it (safety).
- enable LED is not working (can also be a problem with the buffer IC, had some trouble with soldering this buffer). However, even if this LED was working, it would indicate that the board would be disabled (see previous point);
- The 3 I/O headers do not have space for shrouded headers. Instead, I chose to use coloured pin headers to show the different functions of the pins;

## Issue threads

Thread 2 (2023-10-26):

Resistor network size difficult to obtain

Peter-van-Tol, 2023-10-26:
The 1206x4 resistor network is difficult to obtain from AliExpress, or have to revert to Mouser or other supplyers with prohibitive (at least for hobbyist) high prices. These have to be replaced with either smaller components (1206 as total package) or separate resistors.

Peter-van-Tol, 2023-11-06:
Smaller parts might be difficult to solder by hand for DIY-people. Maybe the resistor networks can be duplicated, so for external fabbing the SMD components can be used, while for DIY-enthousiasts the though-hole option is still available.

Peter-van-Tol, 2023-11-06:
Going to be solved in #3

Peter-van-Tol, 2024-01-12:
Solved in version 1.1 of HUB75HAT. Smaller components used, designed to be manufactured by a fab (JLCPCB / PCBWAY / others)

Closed 2024-01-12.

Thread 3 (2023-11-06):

HUB75HAT v1.0: Space around I/O headers insufficient for shrouded header

Peter-van-Tol, 2023-11-06:
The space around the I/O headers is insufficient for shrouded header. In v1.0 this has been solved by applying colored headers showing the functions of the pins. In V1.1 the space should allow for shrouded header:
- The jumpers for power to the connector should be moved down;
- The decoupling capacitors on the power rail should be either moved or flipped to the underside of the board;
- The resistor networks should be either moved or replaced with their through-hole counterpart.

Peter-van-Tol, 2023-11-06:
Going to be solved in #3

Peter-van-Tol, 2024-01-12:
Solved in release [v1. 1] (src/HUB75HAT/releases/v1.1).

Closed 2024-01-12.

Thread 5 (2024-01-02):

Use Release Feature of Github

imvubu, 2024-01-02:
Is it possible to use GitHub releases to segment the various versions of code and board files?

Peter-van-Tol, 2024-01-02:
Thanks for your request. The code is versioned, as it is part of the `litexcnc` codebase and it is placed in the other repository.

A challenge of releasing different versions by GitHub is that this repo contains now 3 boards:
- the HUB75HAT
- the BOB4STEPGEN
- the BOB4ENCODER

It is possible that at one point one of the boards needs an update, while the other remain unchanged. As far as I know, you can have only one release (everything). But if I'm mistaken, please tell me!

How shall the releases be designed:
- by date (everytime a board is updated, all production files will be released);
- by board (each board has its own release history, but not sure whether this is possible)
- other method?

Your input is welcome!

imvubu, 2024-01-11:
Fair point about it containing 3 board,

My request was around wanting to have some boards made and wanting to know knowing that it was past testing

Releases could be based on when a milestone is reached as in you know a board is tested and is working as intended

For me it makes it easier to see what is going on. I may be being a bit pedantic

Peter-van-Tol, 2024-01-11:
At this moment I'm reformatting the repository. Each board will be contained in the `./src` directory and have a dedicated `production` folder in which the production ready versions are published. In the changelog one can see the changes between releases. I expect to finish the work this week.

Peter-van-Tol, 2024-01-11:
Large part of overhaul of the repo is finished. In the README there is a link to latest version of each board.

All current boards have passed testing. Only for HUB75HAT there will be a version 1.2 coming, because the last release there was a problem with the 40-pin header having a clash with a polyfuse. This means that the 40-pin connector has to be soldered manually **and** last, so it rests on top of the polyfuse

Another note is that the HUB75HAT is designed for assembly by JLCPCB (at least, they did it for me, gues other fabs will work similarly). Only the bottom side of the PCB was assembled. The few components remaining on the top side were either unavailable with JLCPCB or very expensive / easy to hand solder.

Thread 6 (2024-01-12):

HUB75HAT V1. 1: 40-pin header clashes with pplyfuses

Peter-van-Tol, 2024-01-12:
40-pin Gpio header has wrong footprint (not shrouded). Therefore the component is clashing with the two polyfuse.

Temporary solved by soldering 40 pin connector on top of polyfuses in order to use the board.

Permanent solution will be correcting the footprint and moving the polyfuses.

Together with this change, the marking CC-NY (license) should be placed on the board again.

Closed 2024-01-13.

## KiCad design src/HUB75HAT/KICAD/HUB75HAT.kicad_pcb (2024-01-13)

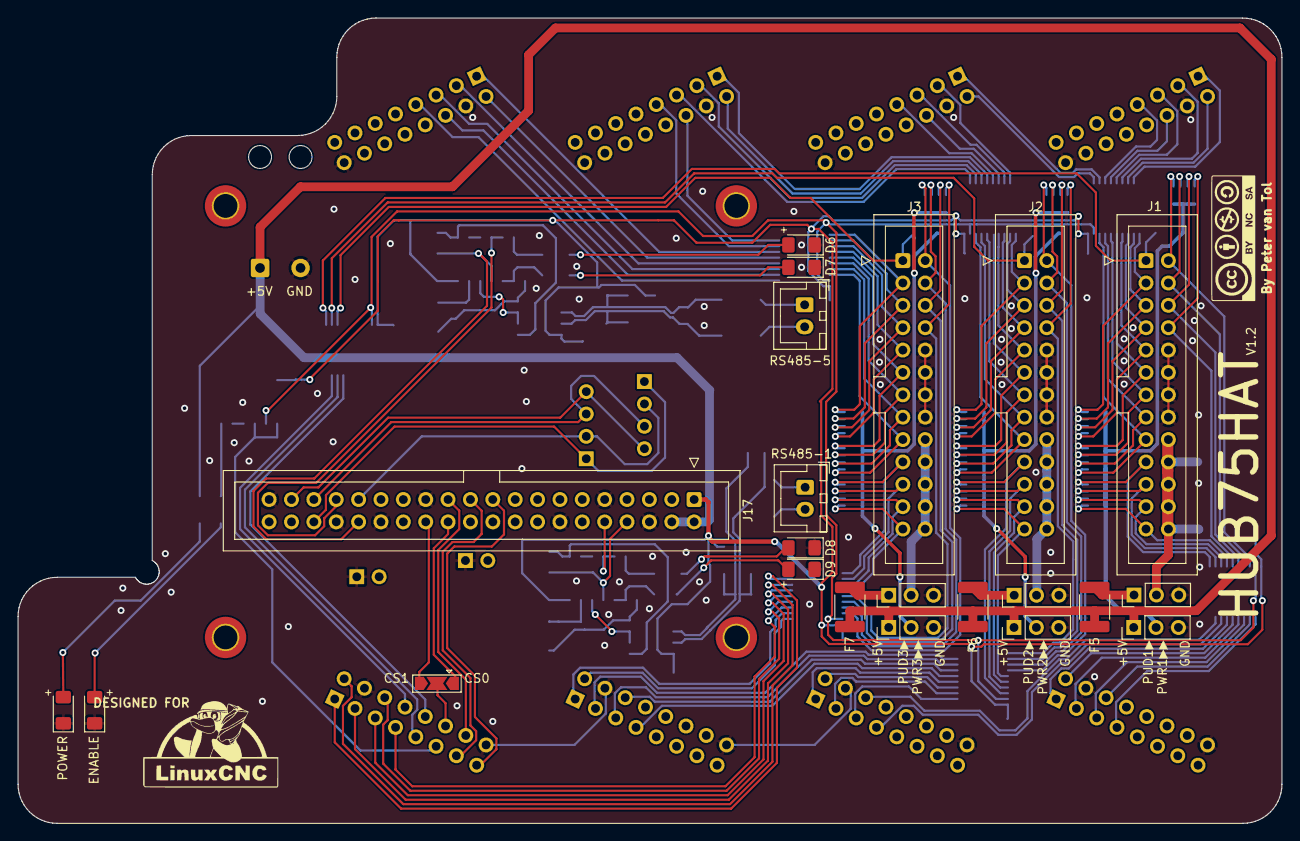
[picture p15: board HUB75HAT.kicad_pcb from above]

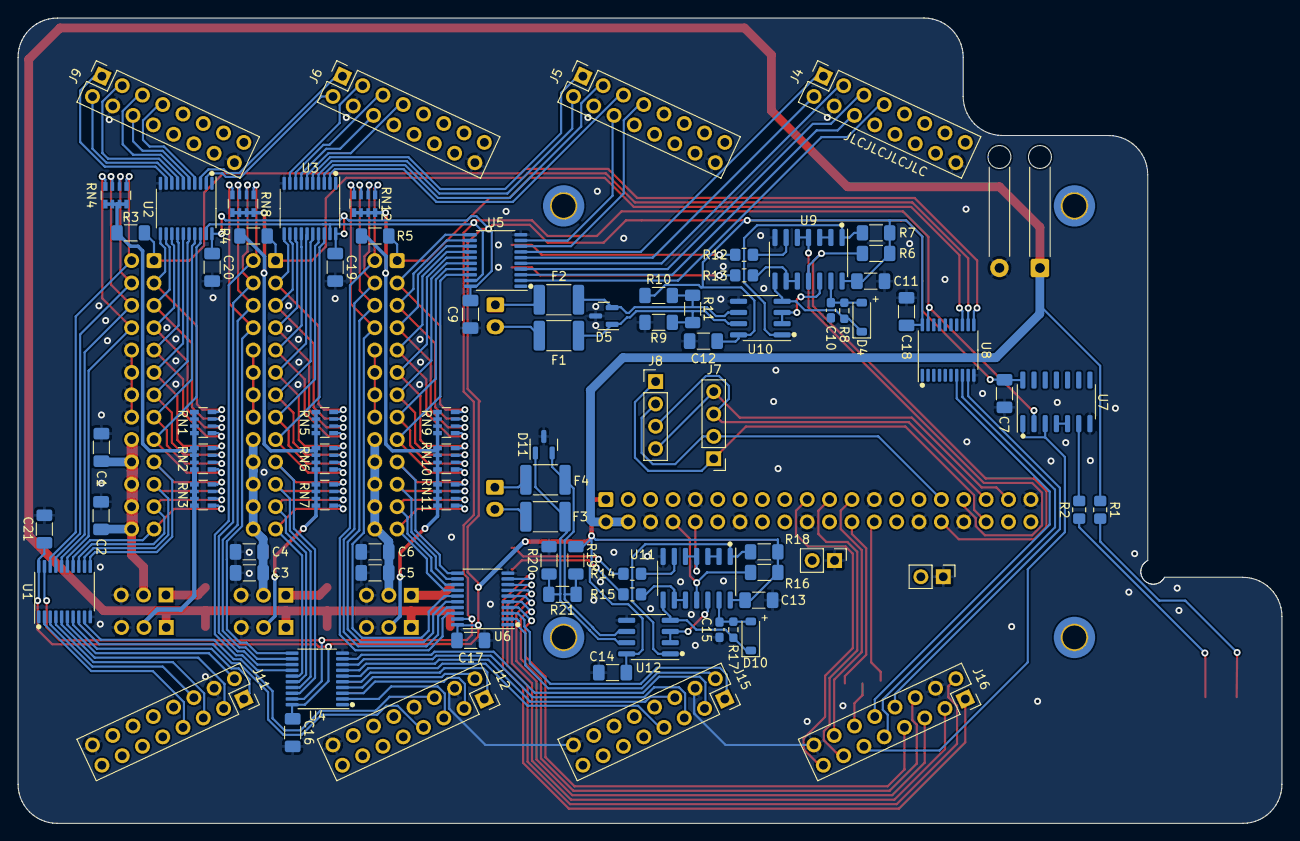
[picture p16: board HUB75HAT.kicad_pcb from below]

Board: 2 copper layers, 143.5 x 91.4 mm, 108 parts (86 on the bottom side), 160 nets.

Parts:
C1, C2, C3, C4, C5, C6, C7, C9, C11, C13, C16, C17, C18, C19, C20, C21: 100nF; C_1206_3216Metric_Pad1.33x1.80mm_HandSolder
C10, C15: 33pF; C_0603_1608Metric_Pad1.08x0.95mm_HandSolder
C12, C14: 0.1uF; C_1206_3216Metric_Pad1.33x1.80mm_HandSolder
D1, D2, D6, D7, D8, D9: LED; LED_1206_3216Metric_Pad1.42x1.75mm_HandSolder
D4, D10: 1N4148W; D_SOD-123
D5, D11: SM712_SOT23; SOT-23
F1, F2, F3, F4, F5, F6, F7: 108L; Fuse_1812_4532Metric_Pad1.30x3.40mm_HandSolder
J1, J2, J3: Conn_02x13_Odd_Even; IDC-Header_2x13_P2.54mm_Vertical
J4, J5, J6, J9, J11, J12, J15, J16: HUB75; PinSocket_2x08_P2.54mm_Vertical
J7: v7.0; PinHeader_1x04_P2.54mm_Vertical
J8: v8.0; PinHeader_1x04_P2.54mm_Vertical
J10: Conn_01x02; SolderWire-0.5sqmm_1x02_P4.6mm_D0.9mm_OD2.1mm_Relief
J13: V7.0; PinHeader_1x02_P2.54mm_Vertical
J14: V8.0; PinHeader_1x02_P2.54mm_Vertical
J17: Conn_02x20_Odd_Even; IDC-Header_2x20_P2.54mm_Vertical
JP1, JP2, JP3, JP4, JP5, JP6: Jumper_3_Open; PinHeader_1x03_P2.54mm_Vertical
JP7: SolderJumper_3_Open; SolderJumper-3_P2.0mm_Open_TrianglePad1.0x1.5mm
R1: 300; R_0805_2012Metric_Pad1.20x1.40mm_HandSolder
R2, R12, R13, R14, R15: 150; R_0805_2012Metric_Pad1.20x1.40mm_HandSolder
R3, R4, R5: R; R_1206_3216Metric_Pad1.30x1.75mm_HandSolder
R6, R16: 4.7k; R_1206_3216Metric_Pad1.30x1.75mm_HandSolder
R7, R9, R10, R18, R19, R20: 4.7K; R_1206_3216Metric_Pad1.30x1.75mm_HandSolder
R8, R17: 56k; R_0603_1608Metric_Pad0.98x0.95mm_HandSolder
R11, R21: 120; R_1206_3216Metric_Pad1.30x1.75mm_HandSolder
RN1, RN2, RN3, RN4, RN5, RN6, RN7, RN8, RN9, RN10, RN11, RN12: CN1J4KTTD1002F; R_Array_Convex_4x0603_handsolder
RS485-1, RS485-5: Conn_01x02_Pin; JST_XH_B2B-XH-A_1x02_P2.50mm_Vertical
U1, U2, U3, U4, U5, U6, U8: 74CB3T3245; TSSOP-20_4.4x6.5mm_P0.65mm
U7, U9, U11: 74HC04; SOIC-14_3.9x8.7mm_P1.27mm
U10, U12: MAX3485; SOIC-8_3.9x4.9mm_P1.27mm

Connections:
+3.3V: C7.1, C9.1, C11.1, C12.1, C13.1, C14.1, C16.1, C17.1, C18.1, C19.1, C20.1, C21.1, J17.1, R6.1, R7.1, R10.1, R16.1, R18.1, R19.1, U1.20 (VCC), U2.20 (VCC), U3.20 (VCC), U4.20 (VCC), U5.20 (VCC), U6.20 (VCC), U7.14 (VCC), U8.20 (VCC), U9.14 (VCC), U10.8 (VCC), U11.14 (VCC), U12.8 (VCC)
+5V: F5.1, F6.1, F7.1, J10.1, J17.2, J17.4, JP4.1 (A), JP5.1 (A), JP6.1 (A), R1.1
/JTAG.TCK: J7.1, J8.1, J17.36
/JTAG.TDI: J7.3, J8.3, J17.35
/JTAG.TDO: J7.4, J8.4, J17.37
/JTAG.TMS: J7.2, J8.2, J17.31
ENA: U1.19 (CE), U2.19 (CE), U3.19 (CE), U4.19 (CE), U5.19 (CE), U6.19 (CE), U7.2, U8.19 (CE)
ENA-LED: R2.1, U7.6
ENA_IN: J16.11, U7.1, U7.3
GND: C1.2, C2.2, C3.2, C4.2, C5.2, C6.2, C7.2, C9.2, C10.2, C11.2, C12.2, C13.2, C14.2, C15.2, C16.2, C17.2, C18.2, C19.2, C20.2, C21.2, D1.1 (K), D2.1 (K), D5.3 (common), D6.1 (K), D7.1 (K), D8.1 (K), D9.1 (K), D11.3 (common), J1.10, J1.12, J1.14, J1.16, J2.10, J2.12, J2.14, J2.16, J3.10, J3.12, J3.14, J3.16, J4.4, J4.16, J5.4, J5.16, J6.4, J6.16, J9.4, J9.16, J10.2, J11.4, J11.16, J12.4, J12.16, J13.1, J14.1, J15.4, J15.16, J16.4, J16.16, J17.6, J17.9, J17.14, J17.20, J17.25, J17.30, J17.34, J17.39, JP1.3 (B), JP2.3 (B), JP3.3 (B), JP4.3 (B), JP5.3 (B), JP6.3 (B), R9.2, R20.2, U1.10 (GND), U2.10 (GND), U3.10 (GND), U4.10 (GND), U5.10 (GND), U6.10 (GND), U7.7 (GND), U8.10 (GND), U9.7 (GND), U10.5 (GND), U11.7 (GND), U12.5 (GND)
J1:0: J11.1, U1.7 (A5)
J1:1: J11.2, U1.6 (A4)
J1:2: J11.3, U1.5 (A3)
J1:4: J11.5, U1.4 (A2)
J1:5: J11.6, U1.3 (A1)
J1:6: J11.7, U1.2 (A0)
J2:0: J12.1, U4.5 (A3)
J2:1: J12.2, U4.4 (A2)
J2:2: J12.3, U4.3 (A1)
J2:4: J12.5, U4.2 (A0)
J2:5: J12.6, U1.9 (A7)
J2:6: J12.7, U1.8 (A6)
J3:0: J15.1, U6.3 (A1)
J3:1: J15.2, U6.2 (A0)
J3:2: J15.3, U4.9 (A7)
J3:4: J15.5, U4.8 (A6)
J3:5: J15.6, U4.7 (A5)
J3:6: J15.7, U4.6 (A4)
J4:0: J16.1, U6.9 (A7)
J4:1: J16.2, U6.8 (A6)
J4:2: J16.3, U6.7 (A5)
J4:4: J16.5, U6.6 (A4)
J4:5: J16.6, U6.5 (A3)
J4:6: J16.7, U6.4 (A2)
J4:7: J16.8, U8.9 (A7)
J4:8: J16.9, U8.8 (A6)
J4:9: J16.10, U8.7 (A5)
J5:0: J4.1, U5.7 (A5)
J5:1: J4.2, U5.6 (A4)
J5:2: J4.3, U5.5 (A3)
J5:4: J4.5, U5.4 (A2)
J5:5: J4.6, U5.3 (A1)
J5:6: J4.7, U5.2 (A0)
J6:0: J5.1, U3.5 (A3)
J6:1: J5.2, U3.4 (A2)
J6:2: J5.3, U3.3 (A1)
J6:4: J5.5, U3.2 (A0)
J6:5: J5.6, U5.9 (A7)
J6:6: J5.7, U5.8 (A6)
J7:0: J6.1, U2.3 (A1)
J7:1: J6.2, U2.2 (A0)
J7:2: J6.3, U3.9 (A7)
J7:4: J6.5, U3.8 (A6)
J7:5: J6.6, U3.7 (A5)
J7:6: J6.7, U3.6 (A4)
J8:0: J9.1, U2.9 (A7)
J8:1: J9.2, U2.8 (A6)
J8:2: J9.3, U2.7 (A5)
J8:4: J9.5, U2.6 (A4)
J8:5: J9.6, U2.5 (A3)
J8:6: J9.7, U2.4 (A2)
unnamed: D1.2 (A), R1.2
unnamed: D2.2 (A), R2.2
unnamed: C10.1, D4.2 (A), R8.2, U9.13
unnamed: D4.1 (K), R8.1, U9.8, U10.4 (DI)
unnamed: D5.1 (A1), F1.1, R9.1, R11.1, U10.7 (B)
unnamed: D5.2 (A2), F2.2, R10.2, R11.2, U10.6 (A)
unnamed: D6.2 (A), R12.2
unnamed: D7.2 (A), R13.2
unnamed: D8.2 (A), R14.2
unnamed: D9.2 (A), R15.2
unnamed: C15.1, D10.2 (A), R17.2, U11.13
unnamed: D10.1 (K), R17.1, U11.8, U12.4 (DI)
unnamed: D11.1 (A1), F3.1, R20.1, R21.1, U12.7 (B)
unnamed: D11.2 (A2), F4.2, R19.2, R21.2, U12.6 (A)
unnamed: F2.1, RS485-5.1
unnamed: F1.2, RS485-5.2
unnamed: F4.1, RS485-1.1
unnamed: F3.2, RS485-1.2
unnamed: F5.2, JP1.1 (A)
unnamed: F6.2, JP2.1 (A)
unnamed: F7.2, JP3.1 (A)
unnamed: JP4.2 (C), R3.2, RN1.1 (R1.1), RN1.2 (R2.1), RN1.3 (R3.1), RN1.4 (R4.1), RN2.1 (R1.1), RN2.2 (R2.1), RN2.3 (R3.1), RN2.4 (R4.1), RN3.1 (R1.1), RN3.2 (R2.1), RN3.3 (R3.1), RN3.4 (R4.1), RN4.1 (R1.1), RN4.2 (R2.1), RN4.3 (R3.1), RN4.4 (R4.1)
unnamed: JP5.2 (C), R4.2, RN5.1 (R1.1), RN5.2 (R2.1), RN5.3 (R3.1), RN5.4 (R4.1), RN6.1 (R1.1), RN6.2 (R2.1), RN6.3 (R3.1), RN6.4 (R4.1), RN7.1 (R1.1), RN7.2 (R2.1), RN7.3 (R3.1), RN7.4 (R4.1), RN8.1 (R1.1), RN8.2 (R2.1), RN8.3 (R3.1), RN8.4 (R4.1)
unnamed: JP6.2 (C), R5.2, RN9.1 (R1.1), RN9.2 (R2.1), RN9.3 (R3.1), RN9.4 (R4.1), RN10.1 (R1.1), RN10.2 (R2.1), RN10.3 (R3.1), RN10.4 (R4.1), RN11.1 (R1.1), RN11.2 (R2.1), RN11.3 (R3.1), RN11.4 (R4.1), RN12.1 (R1.1), RN12.2 (R2.1), RN12.3 (R3.1), RN12.4 (R4.1)
unnamed: R12.1, U9.6
unnamed: R13.1, U9.9, U9.10
unnamed: R14.1, U11.6
unnamed: R15.1, U11.9, U11.10
unnamed: U7.4, U7.5
unnamed: U9.2, U9.3
unnamed: U9.12, U10.2 (~RE), U10.3 (DE)
unnamed: R7.2, U9.1, U10.1 (RO)
unnamed: U11.2, U11.3
unnamed: U11.12, U12.2 (~RE), U12.3 (DE)
unnamed: R18.2, U11.1, U12.1 (RO)
PORTA1: J1.1, R3.1, U8.11 (B7)
PORTA2: J1.3, RN1.8 (R1.2), U2.11 (B7)
PORTA3: J1.5, RN1.7 (R2.2), U2.12 (B6)
PORTA4: J1.7, RN1.6 (R3.2), U2.13 (B5)
PORTA5: J1.9, RN1.5 (R4.2), U2.14 (B4)
PORTA6: J1.11, RN2.8 (R1.2), U2.15 (B3)
PORTA7: J1.13, RN2.7 (R2.2), U2.16 (B2)
PORTA8: J1.15, RN2.6 (R3.2), U2.17 (B1)
PORTA9: J1.17, RN2.5 (R4.2), U2.18 (B0)
PORTA10: J1.19, RN3.8 (R1.2), U1.11 (B7)
PORTA11: J1.21, RN3.7 (R2.2), U1.12 (B6)
PORTA12: J1.23, RN3.6 (R3.2), U1.13 (B5)
PORTA13: J1.25, RN3.5 (R4.2), U1.14 (B4)
PORTA14: J1.2, RN4.5 (R4.2), U1.18 (B0)
PORTA15: J1.4, RN4.6 (R3.2), U1.17 (B1)
PORTA16: J1.6, RN4.7 (R2.2), U1.16 (B2)
PORTA17: J1.8, RN4.8 (R1.2), U1.15 (B3)
PORTB1: J2.1, R4.1, U8.12 (B6)
PORTB2: J2.3, RN5.8 (R1.2), U3.11 (B7)
PORTB3: J2.5, RN5.7 (R2.2), U3.12 (B6)
PORTB4: J2.7, RN5.6 (R3.2), U3.13 (B5)
PORTB5: J2.9, RN5.5 (R4.2), U3.14 (B4)
PORTB6: J2.11, RN6.8 (R1.2), U3.15 (B3)
PORTB7: J2.13, RN6.7 (R2.2), U3.16 (B2)
PORTB8: J2.15, RN6.6 (R3.2), U3.17 (B1)
PORTB9: J2.17, RN6.5 (R4.2), U3.18 (B0)
PORTB10: J2.19, RN7.8 (R1.2), U4.18 (B0)
PORTB11: J2.21, RN7.7 (R2.2), U4.17 (B1)
PORTB12: J2.23, RN7.6 (R3.2), U4.16 (B2)
PORTB13: J2.25, RN7.5 (R4.2), U4.15 (B3)
PORTB14: J2.2, RN8.5 (R4.2), U4.14 (B4)
PORTB15: J2.4, RN8.6 (R3.2), U4.13 (B5)
PORTB16: J2.6, RN8.7 (R2.2), U4.12 (B6)
PORTB17: J2.8, RN8.8 (R1.2), U4.11 (B7)
PORTC1: J3.1, R5.1, U8.13 (B5)
PORTC2: J3.3, RN9.8 (R1.2), U5.11 (B7)
PORTC3: J3.5, RN9.7 (R2.2), U5.12 (B6)
PORTC4: J3.7, RN9.6 (R3.2), U5.13 (B5)
PORTC5: J3.9, RN9.5 (R4.2), U5.14 (B4)
PORTC6: J3.11, RN10.8 (R1.2), U5.15 (B3)
PORTC7: J3.13, RN10.7 (R2.2), U5.16 (B2)
PORTC8: J3.15, RN10.6 (R3.2), U5.17 (B1)
PORTC9: J3.17, RN10.5 (R4.2), U5.18 (B0)
PORTC10: J3.19, RN11.8 (R1.2), U6.11 (B7)
PORTC11: J3.21, RN11.7 (R2.2), U6.12 (B6)
PORTC12: J3.23, RN11.6 (R3.2), U6.13 (B5)
PORTC13: J3.25, RN11.5 (R4.2), U6.14 (B4)
PORTC14: J3.2, RN12.5 (R4.2), U6.18 (B0)
PORTC15: J3.4, RN12.6 (R3.2), U6.17 (B1)
PORTC16: J3.6, RN12.7 (R2.2), U6.16 (B2)
PORTC17: J3.8, RN12.8 (R1.2), U6.15 (B3)
POWOPA: C1.1, C2.1, J1.18, J1.20, J1.22, J1.24, J1.26, JP1.2 (C)
POWOPB: C3.1, C4.1, J2.18, J2.20, J2.22, J2.24, J2.26, JP2.2 (C)
POWOPC: C5.1, C6.1, J3.18, J3.20, J3.22, J3.24, J3.26, JP3.2 (C)
RXD1: J17.10, U11.4, U11.5
RXD5: J17.33, U9.4, U9.5
SPI_CE0: J17.24, JP7.1 (A)
SPI_CE1: J17.26, JP7.3 (B)
SPI_CLCK: J16.14, J17.23
SPI_CS: J16.12, JP7.2 (C)
SPI_MISO: J16.13, J17.21
SPI_MOSI: J16.15, J17.19
TXD1: J17.8, R16.2, U11.11
TXD5: J17.32, R6.2, U9.11

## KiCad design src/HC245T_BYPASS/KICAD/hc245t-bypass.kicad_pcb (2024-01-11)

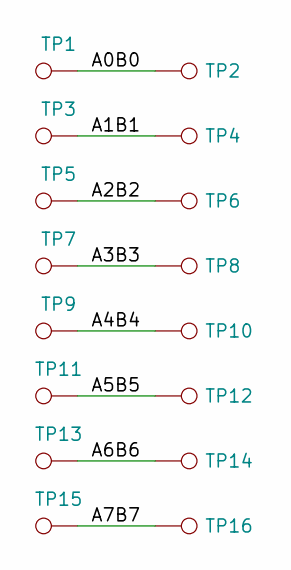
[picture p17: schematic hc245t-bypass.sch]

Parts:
TP1, TP2, TP3, TP4, TP5, TP6, TP7, TP8, TP9, TP10, TP11, TP12, TP13, TP14, TP15, TP16: TestPoint; PAD

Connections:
/A0B0: TP1.1, TP2.1
/A1B1: TP3.1, TP4.1
/A2B2: TP5.1, TP6.1
/A3B3: TP7.1, TP8.1
/A4B4: TP9.1, TP10.1
/A5B5: TP11.1, TP12.1
/A6B6: TP13.1, TP14.1
/A7B7: TP15.1, TP16.1

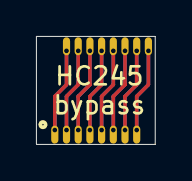
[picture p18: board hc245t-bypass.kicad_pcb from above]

Board: 2 copper layers, 6.6 x 6.0 mm, 16 parts (0 on the bottom side), 8 nets.

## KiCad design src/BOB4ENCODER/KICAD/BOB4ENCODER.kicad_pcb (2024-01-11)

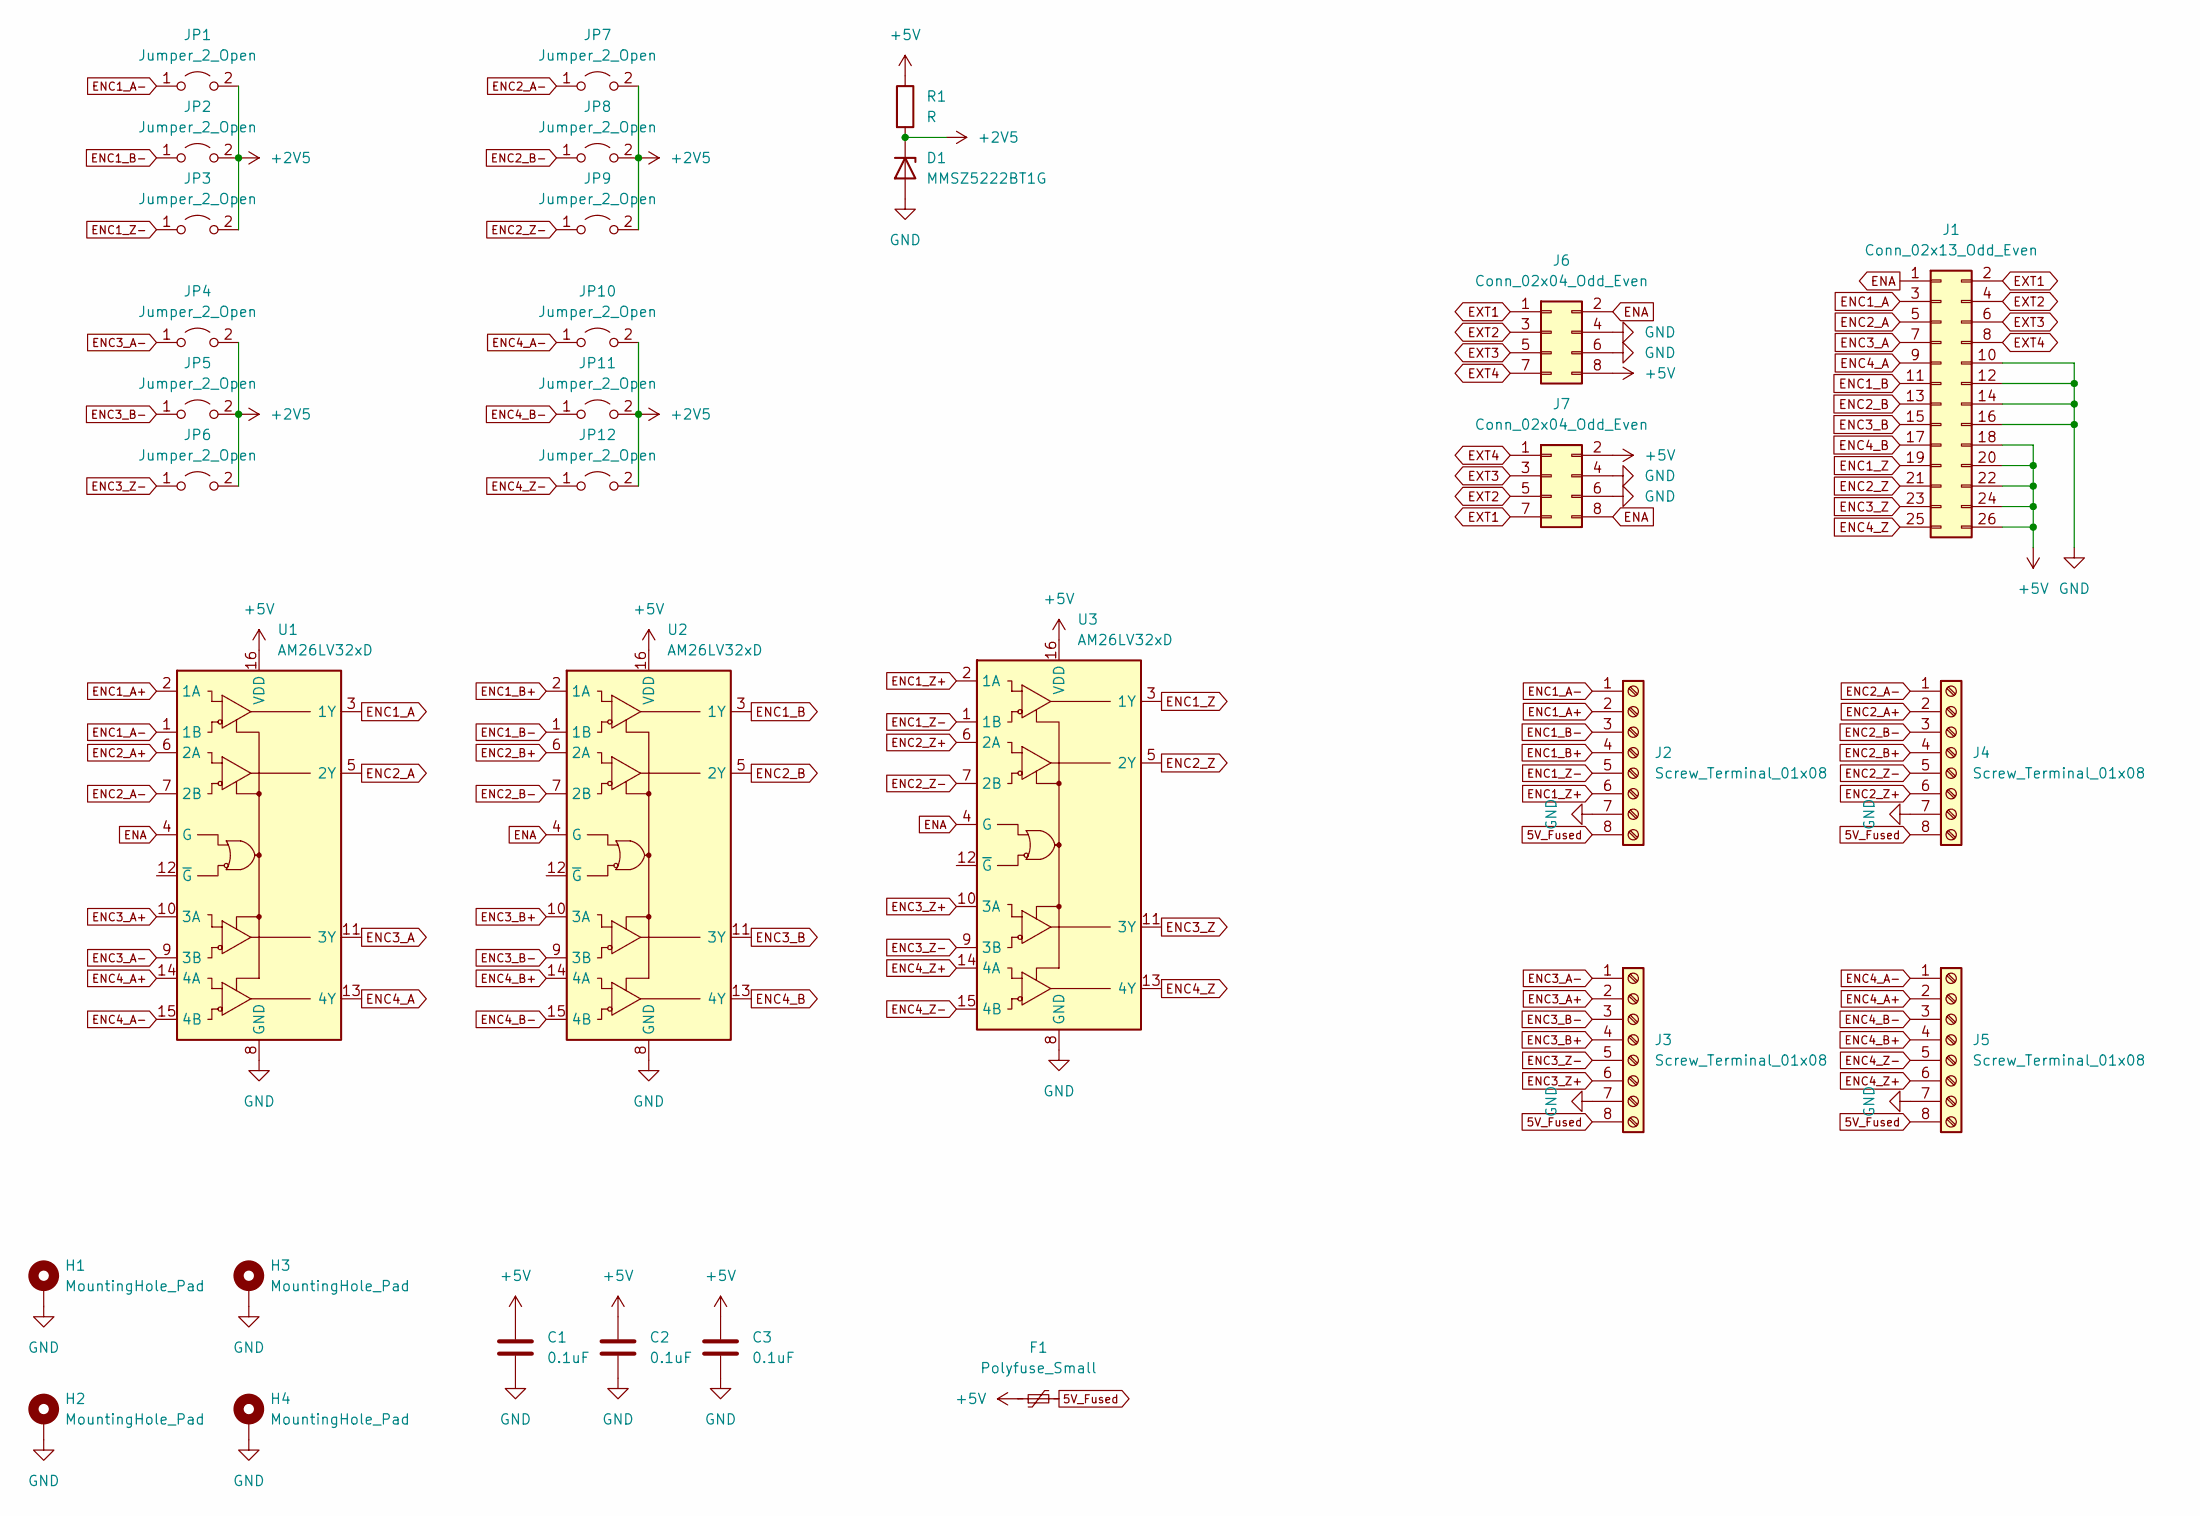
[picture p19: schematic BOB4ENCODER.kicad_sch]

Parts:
C1, C2, C3: 0.1uF; C_1206_3216Metric_Pad1.33x1.80mm_HandSolder
D1: MMSZ5222BT1G; D_SOD-123
F1: Polyfuse_Small; R_1812_4532Metric_Pad1.30x3.40mm_HandSolder
H1, H2, H3, H4: MountingHole_Pad; MountingHole_3.2mm_M3_Pad_Via
J1: Conn_02x13_Odd_Even; IDC-Header_2x13_P2.54mm_Vertical
J2, J3, J4, J5: Screw_Terminal_01x08; CONN-TH_8P-P5.08_KF142V-5.08-8P
J6, J7: Conn_02x04_Odd_Even; PinSocket_2x04_P1.27mm_Horizontal
JP1, JP2, JP3, JP4, JP5, JP6, JP7, JP8, JP9, JP10, JP11, JP12: Jumper_2_Open; PinHeader_1x02_P2.54mm_Vertical
R1: R; R_1206_3216Metric_Pad1.30x1.75mm_HandSolder
U1, U2, U3: AM26LV32xD; SOIC-16_3.9x9.9mm_P1.27mm

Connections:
5V_Fused: F1.2, J2.8, J3.8, J4.8, J5.8
+2V5: D1.1 (K), JP1.2 (B), JP2.2 (B), JP3.2 (B), JP4.2 (B), JP5.2 (B), JP6.2 (B), JP7.2 (B), JP8.2 (B), JP9.2 (B), JP10.2 (B), JP11.2 (B), JP12.2 (B), R1.2
+5V: C1.1, C2.1, C3.1, F1.1, J1.18, J1.20, J1.22, J1.24, J1.26, J6.8, J7.2, R1.1, U1.16 (VDD), U2.16 (VDD), U3.16 (VDD)
ENA: J1.1, J6.2, J7.8, U1.4 (G), U2.4 (G), U3.4 (G)
ENC1_A: J1.3, U1.3 (1Y)
ENC1_A+: J2.2, U1.2 (1A)
ENC1_A-: J2.1, JP1.1 (A), U1.1 (1B)
ENC1_B: J1.11, U2.3 (1Y)
ENC1_B+: J2.4, U2.2 (1A)
ENC1_B-: J2.3, JP2.1 (A), U2.1 (1B)
ENC1_Z: J1.19, U3.3 (1Y)
ENC1_Z+: J2.6, U3.2 (1A)
ENC1_Z-: J2.5, JP3.1 (A), U3.1 (1B)
ENC2_A: J1.5, U1.5 (2Y)
ENC2_A+: J4.2, U1.6 (2A)
ENC2_A-: J4.1, JP7.1 (A), U1.7 (2B)
ENC2_B: J1.13, U2.5 (2Y)
ENC2_B+: J4.4, U2.6 (2A)
ENC2_B-: J4.3, JP8.1 (A), U2.7 (2B)
ENC2_Z: J1.21, U3.5 (2Y)
ENC2_Z+: J4.6, U3.6 (2A)
ENC2_Z-: J4.5, JP9.1 (A), U3.7 (2B)
ENC3_A: J1.7, U1.11 (3Y)
ENC3_A+: J3.2, U1.10 (3A)
ENC3_A-: J3.1, JP4.1 (A), U1.9 (3B)
ENC3_B: J1.15, U2.11 (3Y)
ENC3_B+: J3.4, U2.10 (3A)
ENC3_B-: J3.3, JP5.1 (A), U2.9 (3B)
ENC3_Z: J1.23, U3.11 (3Y)
ENC3_Z+: J3.6, U3.10 (3A)
ENC3_Z-: J3.5, JP6.1 (A), U3.9 (3B)
ENC4_A: J1.9, U1.13 (4Y)
ENC4_A+: J5.2, U1.14 (4A)
ENC4_A-: J5.1, JP10.1 (A), U1.15 (4B)
ENC4_B: J1.17, U2.13 (4Y)
ENC4_B+: J5.4, U2.14 (4A)
ENC4_B-: J5.3, JP11.1 (A), U2.15 (4B)
ENC4_Z: J1.25, U3.13 (4Y)
ENC4_Z+: J5.6, U3.14 (4A)
ENC4_Z-: J5.5, JP12.1 (A), U3.15 (4B)
EXT1: J1.2, J6.1, J7.7
EXT2: J1.4, J6.3, J7.5
EXT3: J1.6, J6.5, J7.3
EXT4: J1.8, J6.7, J7.1
GND: C1.2, C2.2, C3.2, D1.2 (A), H1.1, H2.1, H3.1, H4.1, J1.10, J1.12, J1.14, J1.16, J2.7, J3.7, J4.7, J5.7, J6.4, J6.6, J7.4, J7.6, U1.8 (GND), U2.8 (GND), U3.8 (GND)

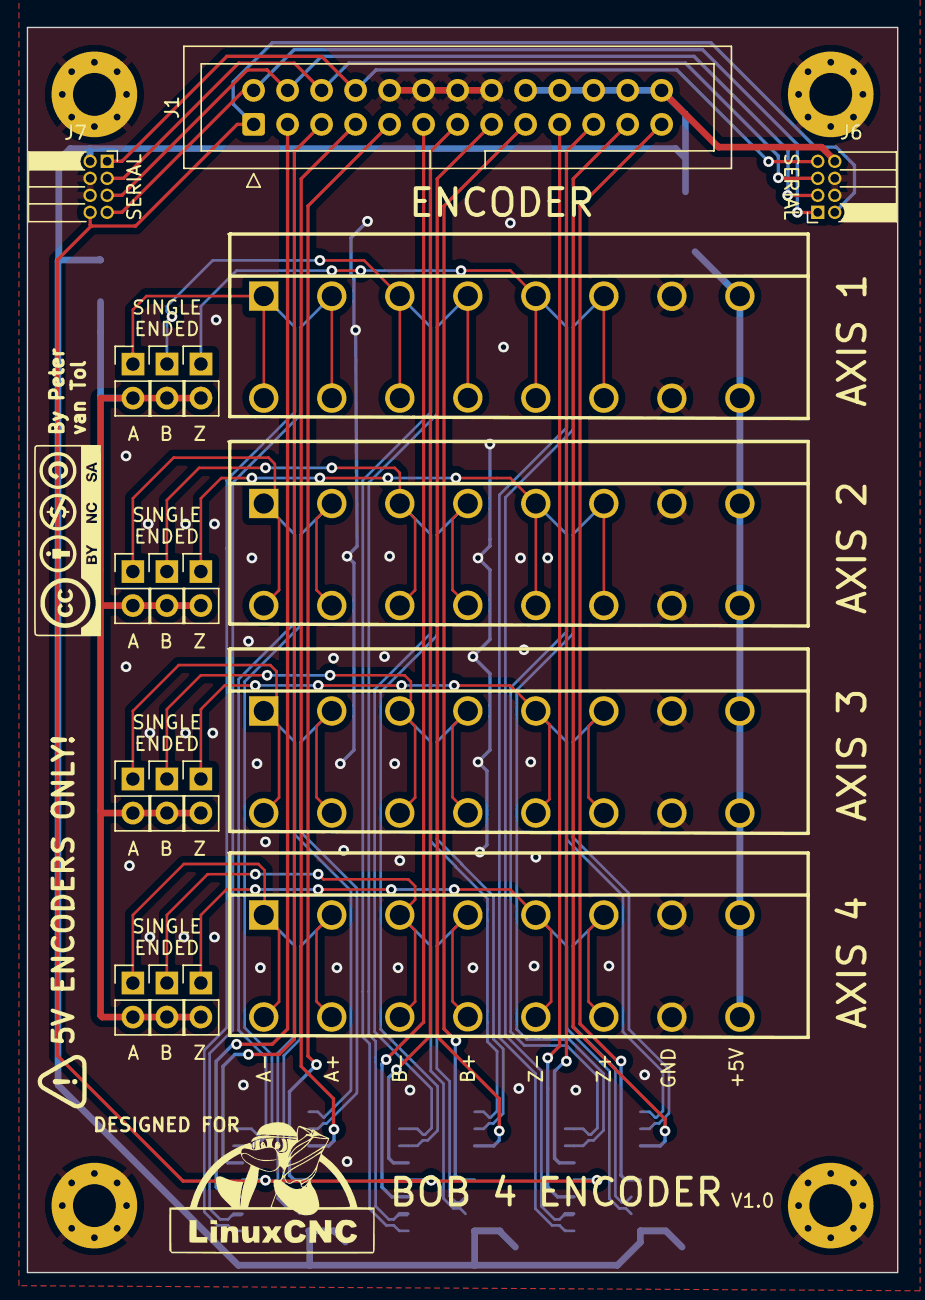
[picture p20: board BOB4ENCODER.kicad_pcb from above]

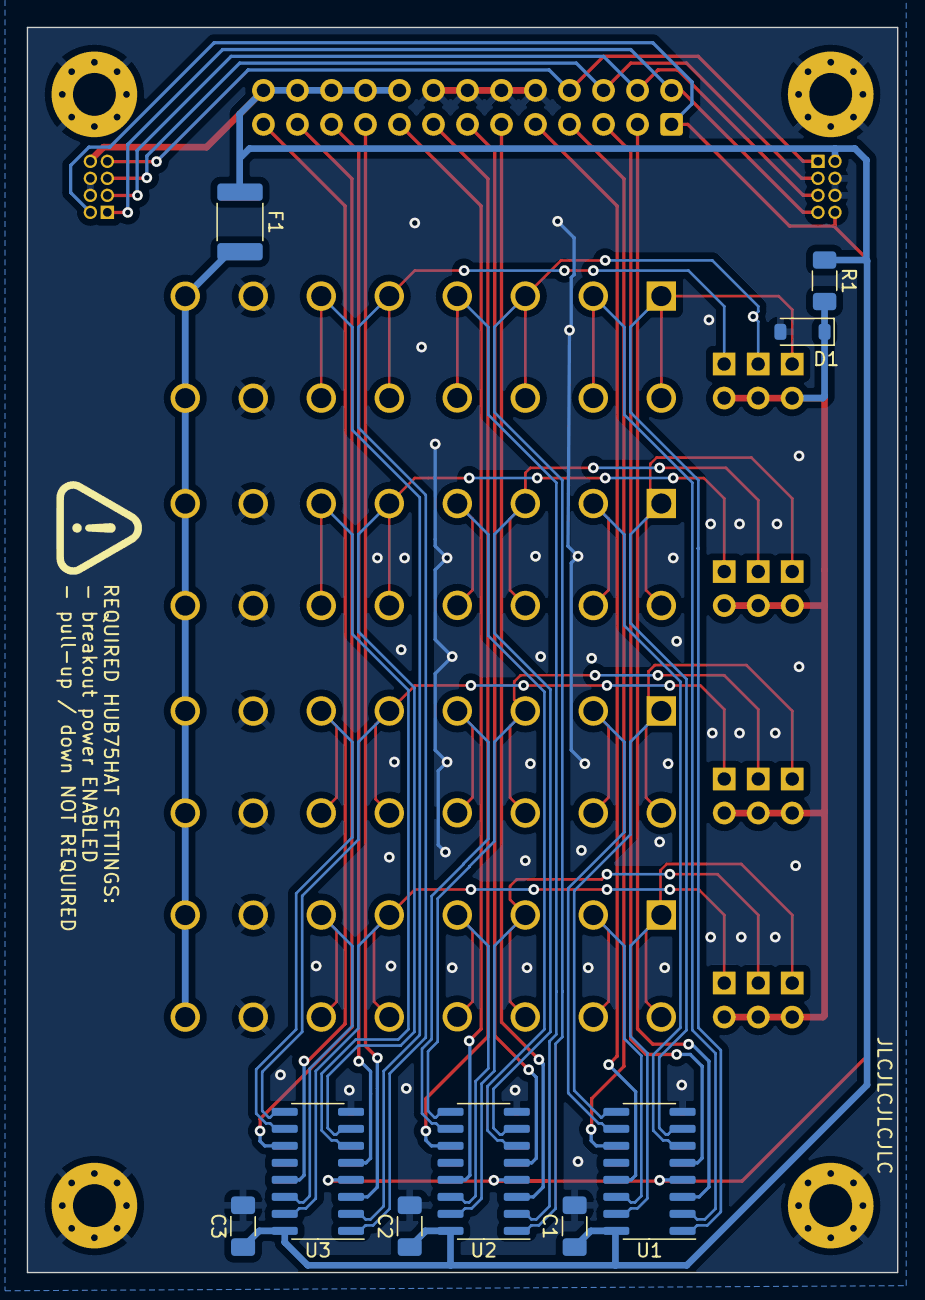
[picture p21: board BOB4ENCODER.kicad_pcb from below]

Board: 2 copper layers, 65.0 x 93.0 mm, 32 parts (9 on the bottom side), 45 nets.

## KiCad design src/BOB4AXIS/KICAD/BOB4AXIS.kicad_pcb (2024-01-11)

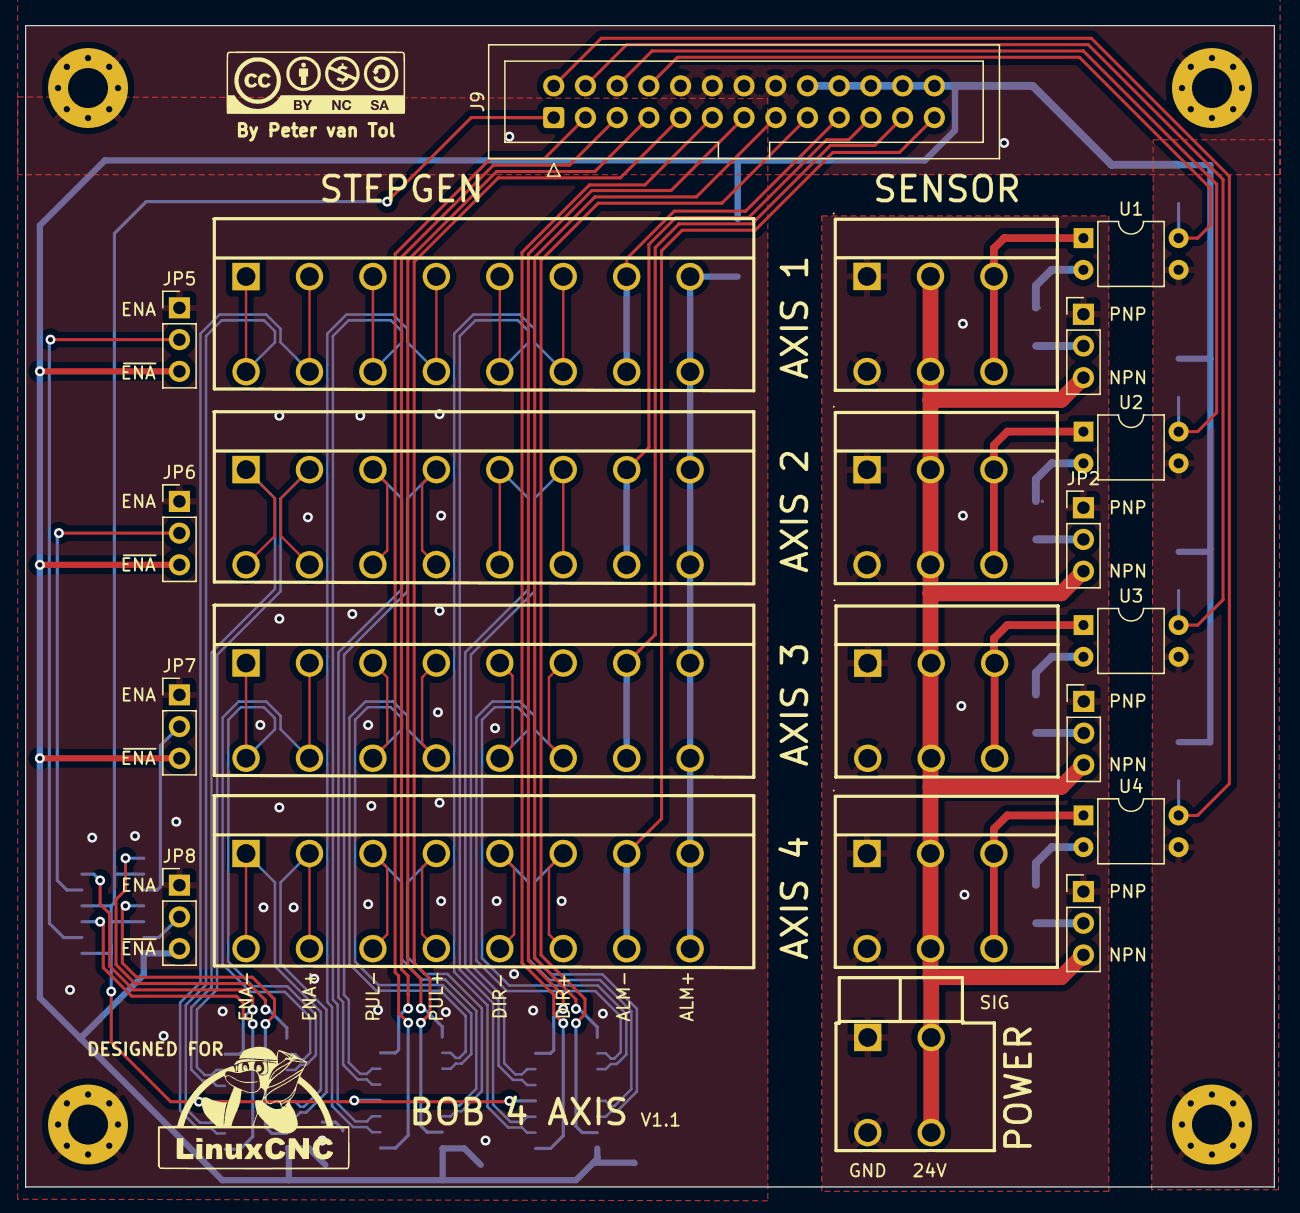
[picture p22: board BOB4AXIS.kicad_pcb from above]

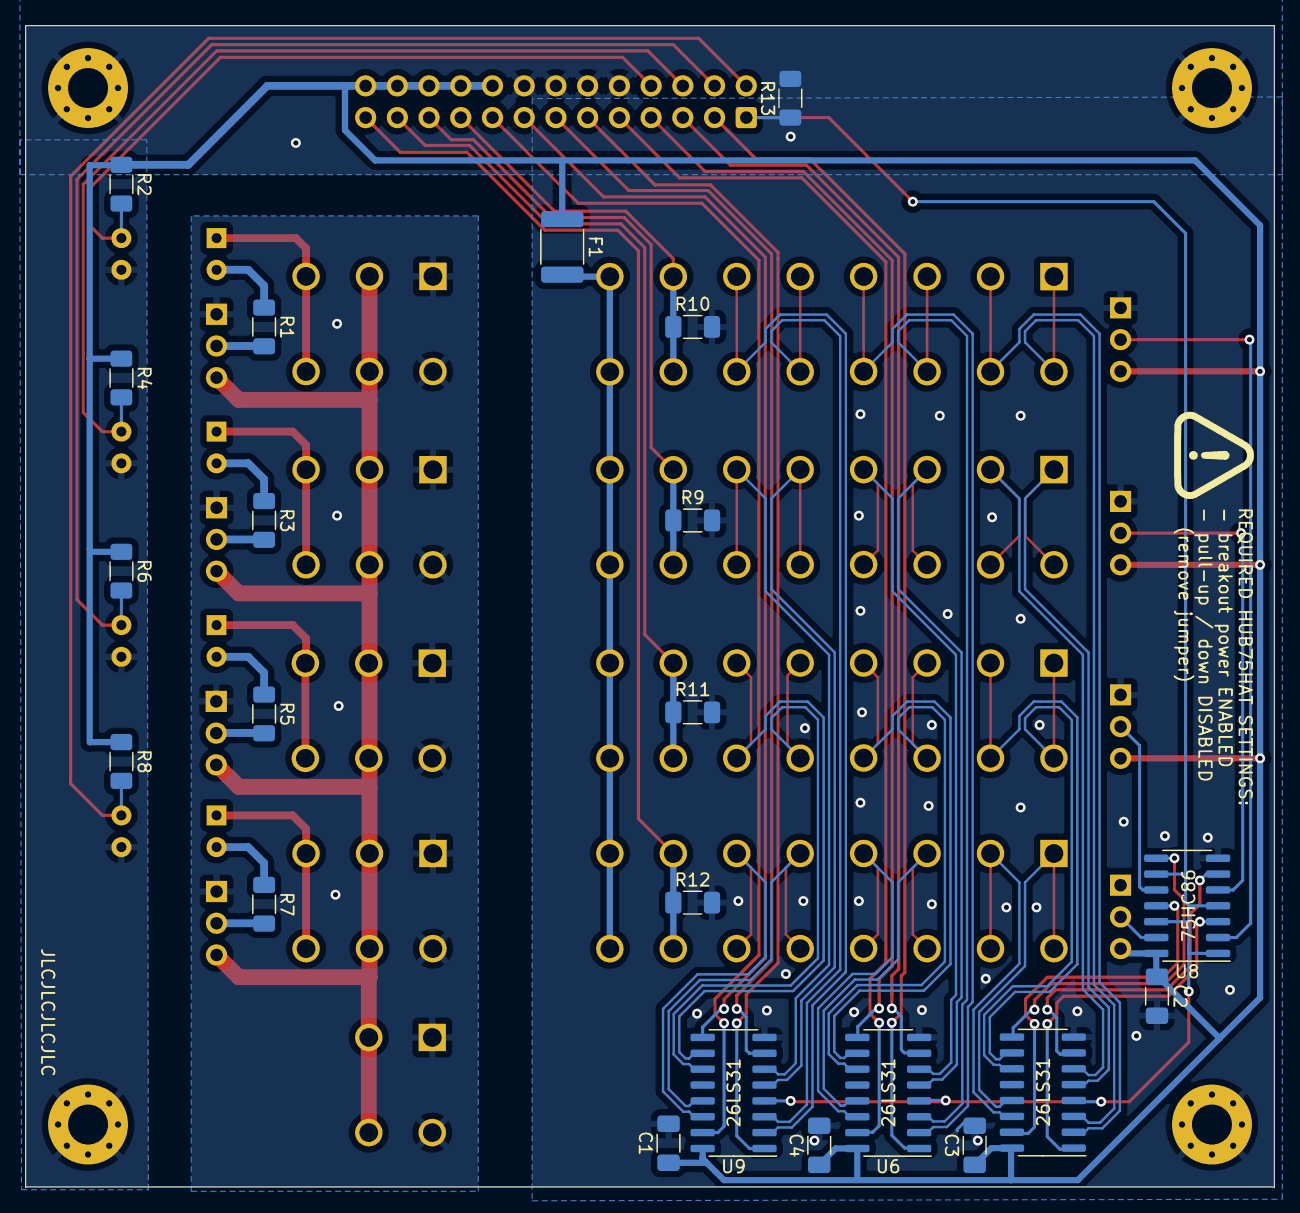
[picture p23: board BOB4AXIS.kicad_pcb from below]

Board: 2 copper layers, 100.0 x 93.0 mm, 48 parts (22 on the bottom side), 66 nets.

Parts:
C1, C2, C3, C4: 0.1uF; C_1206_3216Metric_Pad1.33x1.80mm_HandSolder
F1: Polyfuse_Small; R_1812_4532Metric_Pad1.30x3.40mm_HandSolder
H1, H2, H3, H4: MountingHole_Pad; MountingHole_3.2mm_M3_Pad_Via
J1, J2, J3, J4: Screw_Terminal_01x03; CONN-TH_3P-P5.08_KF142V-5.08-3P
J5, J6, J7, J8: Screw_Terminal_01x08; CONN-TH_8P-P5.08_KF142V-5.08-8P
J9: Conn_02x13_Odd_Even; IDC-Header_2x13_P2.54mm_Vertical
JP1, JP2, JP3, JP4, JP5, JP6, JP7, JP8: Jumper_3_Open; PinHeader_1x03_P2.54mm_Vertical
R1, R3, R5: 1k; R_1206_3216Metric_Pad1.30x1.75mm_HandSolder
R2, R4, R6, R8, R9, R10, R11, R12, R13: 10k; R_1206_3216Metric_Pad1.30x1.75mm_HandSolder
R7: R; R_1206_3216Metric_Pad1.30x1.75mm_HandSolder
U1, U2, U3, U4: LTV-814; DIP-4_W7.62mm
U5, U6, U9: AM26LS31CD; SOIC-16_3.9x9.9mm_P1.27mm
U7: KF142V-5_08-2P; CONN-TH_P5.08_KF142V-5.08-2P
U8: 74HC86; SOIC-14_3.9x8.7mm_P1.27mm

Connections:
5V_Fused: F1.2, J5.8, J6.8, J7.8, J8.8
+5V: C1.1, C2.1, C3.1, C4.1, F1.1, J9.18, J9.20, J9.22, J9.24, J9.26, JP5.3 (B), JP6.3 (B), JP7.3 (B), JP8.3 (B), R2.1, R4.1, R6.1, R8.1, U5.16 (VDD), U6.16 (VDD), U8.14 (VCC), U9.16 (VDD)
+24V: J1.2, J2.2, J3.2, J4.2, JP1.3 (B), JP2.3 (B), JP3.3 (B), JP4.3 (B), U7.1
ALARM1: J5.7, J9.19, R10.1
ALARM2: J6.7, J9.21, R9.1
ALARM3: J7.7, J9.23, R11.1
ALARM4: J8.7, J9.25, R12.1
DIR1: J9.11, U9.1 (1A)
DIR1+: J5.6, U9.2 (1Y)
DIR1-: J5.5, U9.3 (1Z)
DIR2: J9.13, U9.7 (2A)
DIR2+: J6.6, U9.6 (2Y)
DIR2-: J6.5, U9.5 (2Z)
DIR3: J9.15, U9.9 (3A)
DIR3+: J7.6, U9.10 (3Y)
DIR3-: J7.5, U9.11 (3Z)
DIR4: J9.17, U9.15 (4A)
DIR4+: J8.6, U9.14 (4Y)
DIR4-: J8.5, U9.13 (4Z)
ENA: J9.1, R13.1, U5.4 (G), U6.4 (G), U8.1, U8.4, U8.9, U8.12, U9.4 (G)
ENA1: U5.1 (1A), U8.3
ENA1+: J5.2, U5.2 (1Y)
ENA1-: J5.1, U5.3 (1Z)
ENA2: U5.7 (2A), U8.6
ENA2+: J6.2, U5.6 (2Y)
ENA2-: J6.1, U5.5 (2Z)
ENA3: U5.9 (3A), U8.8
ENA3+: J7.2, U5.10 (3Y)
ENA3-: J7.1, U5.11 (3Z)
ENA4: U5.15 (4A), U8.11
ENA4+: J8.2, U5.14 (4Y)
ENA4-: J8.1, U5.13 (4Z)
GND: C1.2, C2.2, C3.2, C4.2, H1.1, H2.1, H3.1, H4.1, J9.10, J9.12, J9.14, J9.16, JP5.1 (A), JP6.1 (A), JP7.1 (A), JP8.1 (A), R9.2, R10.2, R11.2, R12.2, R13.2, U1.3, U2.3, U3.3, U4.3, U5.8 (GND), U6.8 (GND), U8.7 (GND), U9.8 (GND)
GND1: J1.1, J2.1, J3.1, J4.1, JP1.1 (A), JP2.1 (A), JP3.1 (A), JP4.1 (A), U7.2
HOME1: J9.8, R2.2, U1.4
HOME2: J9.6, R4.2, U2.4
HOME3: J9.4, R6.2, U3.4
HOME4: J9.2, R8.2, U4.4
unnamed: J1.3, U1.1
unnamed: J2.3, U2.1
unnamed: J3.3, U3.1
unnamed: J4.3, U4.1
unnamed: JP1.2 (C), R1.2
unnamed: JP2.2 (C), R3.2
unnamed: JP3.2 (C), R5.2
unnamed: JP4.2 (C), R7.2
unnamed: JP5.2 (C), U8.2
unnamed: JP6.2 (C), U8.5
unnamed: JP7.2 (C), U8.10
unnamed: JP8.2 (C), U8.13
unnamed: R1.1, U1.2
unnamed: R3.1, U2.2
unnamed: R5.1, U3.2
unnamed: R7.1, U4.2
STEP1: J9.3, U6.1 (1A)
STEP1+: J5.4, U6.2 (1Y)
STEP1-: J5.3, U6.3 (1Z)
STEP2: J9.5, U6.7 (2A)
STEP2+: J6.4, U6.6 (2Y)
STEP2-: J6.3, U6.5 (2Z)
STEP3: J9.7, U6.9 (3A)
STEP3+: J7.4, U6.10 (3Y)
STEP3-: J7.3, U6.11 (3Z)
STEP4: J9.9, U6.15 (4A)
STEP4+: J8.4, U6.14 (4Y)
STEP4-: J8.3, U6.13 (4Z)

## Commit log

2023-09-18 Finished first versiom
    [IO.kicad_sch, LITEXCNC-HUB75HAT.kicad_pcb, LITEXCNC-HUB75HAT.kicad_sch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]
2023-09-18 Initial commit documentation
    [IO1.csv, IO2.csv, IO3.csv]
2023-09-30 Proto-type board finished
    [IO.kicad_sch, LITEXCNC-HUB75HAT-backup.kicad_pcb, LITEXCNC-HUB75HAT.kicad_pcb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]
2023-10-16 Prototype ordered
    [BOM-LITEXCNC-HUB75HAT.csv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]
2023-10-27 Decoupling capacitors
    [BOB4AXIS.kicad_pcb, BOB4AXIS.kicad_sch]
2023-10-27 Updated production files
    [BOB4AXIS-CuBottom.gbr, BOB4AXIS-CuTop.gbr, BOB4AXIS-EdgeCuts.gbr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]
2023-10-29 Small (non-functional) updates
    [BOB4ENCODER.kicad_pcb, BOB4ENCODER.kicad_sch]
2023-11-19 Version 1.1
    [BOM-LITEXCNC-HUB75HAT.csv, IO.kicad_sch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]
2023-11-19 Added power + pull-up
2023-11-19 Added UART, removed OpenOCD
2023-11-19 Updated labels
    [LITEXCNC-HUB75HAT-CuBottom.gbr, LITEXCNC-HUB75HAT-CuTop.gbr, LITEXCNC-HUB75HAT-EdgeCuts.gbr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]
2024-01-09 Moving to new structure
    [BOB4AXIS-CuBottom.gbr, BOB4AXIS-CuTop.gbr, BOB4AXIS-EdgeCuts.gbr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]
2024-01-11 Add pull-down resistor on ENA
    [BOB4AXIS.kicad_pcb, BOB4AXIS.kicad_sch]
2024-01-11 BOB4AXIS: release v1.0
    [BOB4AXIS-CuBottom.gbr, BOB4AXIS-CuTop.gbr, BOB4AXIS-EdgeCuts.gbr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]
2024-01-11 BOB4AXIS: release v1.1
    [BOB4AXIS-CuBottom.gbr, BOB4AXIS-CuTop.gbr, BOB4AXIS-EdgeCuts.gbr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]
2024-01-11 Remove old production files
    [BOB4AXIS-CuBottom.gbr, BOB4AXIS-CuTop.gbr, BOB4AXIS-EdgeCuts.gbr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]
2024-01-11 Update latest version
    [BOB4ENCODER.kicad_pcb, BOB4ENCODER.kicad_sch]
2024-01-11 BOB4ENCODER: release v1.0
    [BOB4ENCODER-CuBottom.gbr, BOB4ENCODER-CuTop.gbr, BOB4ENCODER-EdgeCuts.gbr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]
2024-01-11 Version 1.1 produced
    [LITEXCNC-HUB75HAT.kicad_pcb]
2024-01-11 HUB75HAT: release version 1.0
    [BOM-LITEXCNC-HUB75HAT.csv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]
2024-01-11 HUB75HAT: release version 1.1
    [BOM-HUB75HAT.csv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]
2024-01-11 HC245T_BYPASS: Initial commit
    [hc245t-bypass-panel-CuBottom.gbr, hc245t-bypass-panel-CuTop.gbr, hc245t-bypass-panel-EdgeCuts.gbr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]
2024-01-11 Corrected uart number
2024-01-13 Solved problem with J17 (GPIO header)
    [LITEXCNC-HUB75HAT.kicad_pcb, LITEXCNC-HUB75HAT.kicad_sch]
2024-01-13 Renamed / removing prefix LITEXCNC
    [HUB75HAT.kicad_pcb, HUB75HAT.kicad_sch, IO.kicad_sch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]
2024-01-13 Release v1.2
    [BOM-HUB75HAT.csv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]
2024-01-13 Update after save (rounding)
    [HUB75HAT.kicad_pcb]
